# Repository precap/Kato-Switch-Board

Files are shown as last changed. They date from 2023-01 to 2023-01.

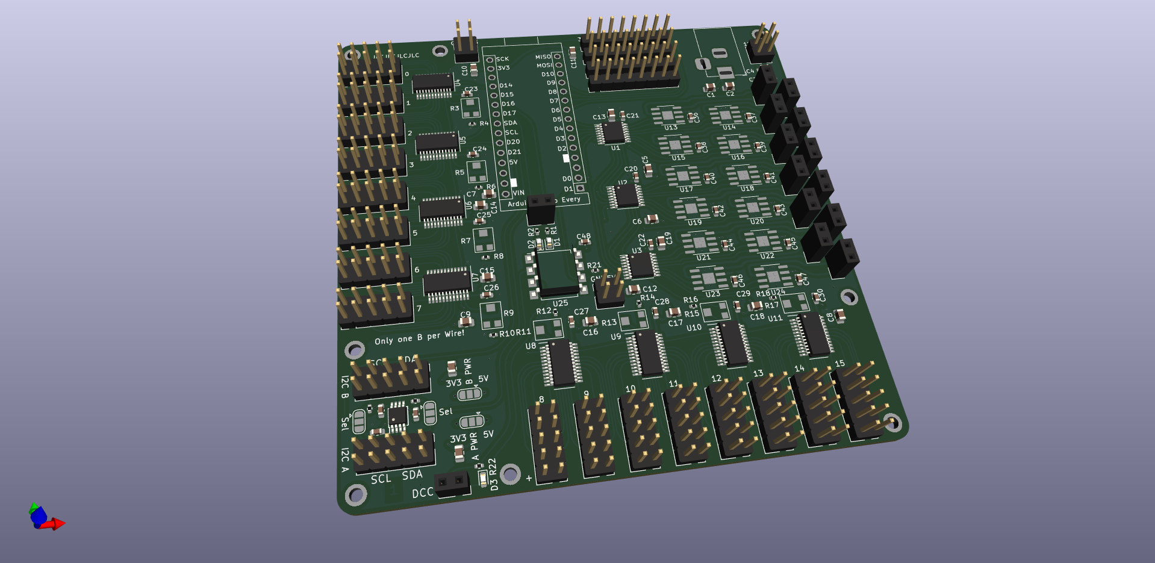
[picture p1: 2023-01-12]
kato-switch-board.png

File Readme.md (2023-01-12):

The board is designed to throw single solenoid switches (e.g. Kato N-scale switches), and serve as multipurpose Expansion to a DCC-EX setup.

# Software
to be written. Help welcome.

# Hardware
Created in KiCad 6.10. Supposedly all the symbol libraries are included in KiCad 6 Projects. I have never tested that though, so let me know if there are any problems with loading.

## Arduino Nano Every
The Board is designed to run with an Arduino Nano Every exclusively (Note: Arduino Nano Every is distinct from Arduino Nano).
This is a conscious Design Decision, as the Nano Every has all the power supply components on board to generate sufficient 3.3V and 5V amperage to power the entire board from the higher Voltage input over the Barrel Jack.
Warning: Do not attempt to run Arduino Nano or other pin compatible boards that cannot handle high voltage on the VIN pin.

## Power Supply
should be provided to the 2.1mm Barrel Jack, or to the pins beside it marked 12V. Voltage fed here will go directly to the switches, LEDs, and to the VIN pin in the Arduino Nano Footprint.
The Arduino Nano Every can provide 1A of 5V, and up to 0.5A of that can further be converted to 3.3V. Most of this capability will be unused and is made available on the marked 2x2 pin headers for external use.

## Board Features
### Switches
Support for 12 Switches. Switching is performed by PT5126A-H chips. Supposedly they can manage up to 2.8A (Kato Switch will draw 0.5A@12V, Double crossover 2A).
Connectors are standard 1x2 pins with 2.54mm spacing for now.

### LED
Up to 128 Output pins. Using SM16206S, which seem to be a knockoff of the (magnitudes more expensive) TLC59282DBQR.
The outermst pins on the connectors are power supply, the others connected to the outputs.

### I2C
A PCA9617ADPJ i2c repeater is fitted on the board, allowing the i2c bus to reach a greater area. The chip can also translate between different voltage levels on the i2c bus, jumpers to set the voltage are provided.

### DCC
DCC Input over an optocopler is possible.

### RFID
Up to four RC522 RFID Reader breakout boards can be connected. The pin arrangement matches commonly found breakout boards, allowing connection with a 8 pin cable.
Whether this feature is can be added to the software in a way that supports all 4 readers remains to be seen, as the RC522 must be polled continuously to detect passing RFID Tags.

## Evaluation Testing

All Evaluation Testing was only performed in a feature incomplete Prototype Version.

| Component | Status |
|---|---|
| Switch Drivers| OK |
| LED Drivers | tbd |
| I2C Repeater  | OK |
| DCC Circuitry | no hw  |
| RFID Reader | OK |

# Production
All SMD Components are available @ jlcpcb at time of release.
Production files can be found in `jlcbcb-production/`. Only the SMD-only assembly files are complete at time of release.
10 boards, assembled with SMD Coponents only, are around 125$ before shipping and taxes. Placing all the Pins will push this to 200$.

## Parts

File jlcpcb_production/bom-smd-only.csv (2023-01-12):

Designator | Footprint | Comment | LCSC Part Number
C1, C2, C3, C31, C35, C4, C5, C6, C7, C8, C9 | 0805 | 22u | C45783
C10, C11, C12, C13, C14, C15, C16, C17, C18, C19 | 0805 | 47u | C16780
C20, C21, C22, C23, C24, C25, C26, C27, C28, C29, C30, C32, C33, C34, C36, C37, C38, C39, C40, C41, C42, C43, C44, C45, C46, C47, C48 | 0603 | 100nf | C14663
D1, D2, D3 | 0603 | 0603_LED | C72043
R1, R10, R12, R14, R16, R18, R2, R22, R4, R6, R8 | 0402 | 2k2 | C25879
R11, R13, R15, R17, R3, R5, R7, R9 | SMD | VG039NCHXTB503 | C145161
R19, R20, R21 | 0402 | 10k | C25744
U1, U2, U3 | TSSOP-16 | 74HC238 | C60434
U10, U11, U4, U5, U6, U7, U8, U9 | QSOP-24 | SM16206 | C121618
U12 | TSSOP-8 | PCA9617ADPJ | C128388
U13, U14, U15, U16, U17, U18, U19, U20, U21, U22, U23, U24 | HSOP-8-1 | PT5126A | C782185
U25 | SSO-8 | 6N137 | C110020

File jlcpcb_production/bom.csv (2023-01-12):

Designator | Footprint | Comment | LCSC Part Number
C1, C2, C3, C31, C35, C4, C5, C6, C7, C8, C9 | 805 | 22u | C45783
C10, C11, C12, C13, C14, C15, C16, C17, C18, C19 | 805 | 47u | C16780
C20, C21, C22, C23, C24, C25, C26, C27, C28, C29, C30, C32, C33, C34, C36, C37, C38, C39, C40, C41, C42, C43, C44, C45, C46, C47, C48 | 603 | 100nf | C14663
D1, D2, D3 | 603 | 0603_LED | C72043
R1, R10, R12, R14, R16, R18, R2, R22, R4, R6, R8 | 402 | 2k2 | C25879
R11, R13, R15, R17, R3, R5, R7, R9 | SMD | VG039NCHXTB503 | C145161
R19, R20, R21 | 402 | 10k | C25744
U1, U2, U3 | TSSOP-16 | 74HC238 | C60434
U10, U11, U4, U5, U6, U7, U8, U9 | QSOP-24 | SM16206 | C121618
U12 | TSSOP-8 | PCA9617ADPJ | C128388
U13, U14, U15, U16, U17, U18, U19, U20, U21, U22, U23, U24 | HSOP-8-1 | PT5126A | C782185
U25 | SSO-8 | 6N137 | C110020
J1, J2, J3, J4 | PinHeader_1x08_P2.54mm_Vertical | Conn_01x08 | C358689
J10, J11, J12, J13, J14, J15, J16, J17, J18, J19, J20, J21, J22, J23, J24, J25, J26, J27 | PinHeader_2x05_P2.54mm_Vertical | Conn_02x05_Odd_Even | C492422
J28, J29, J30, J31, J32, J33, J34, J35, J36, J37, J38, J39, J40, J5 | PinSocket_1x02_P2.54mm_Vertical | Conn_01x02 | C492401
J6 | BarrelJack_Horizontal | Barrel_Jack_MountingPin | C16214
A1, A2 | PinHeader_1x15_P2.54mm_Vertical | Arduino Nano | C2932676

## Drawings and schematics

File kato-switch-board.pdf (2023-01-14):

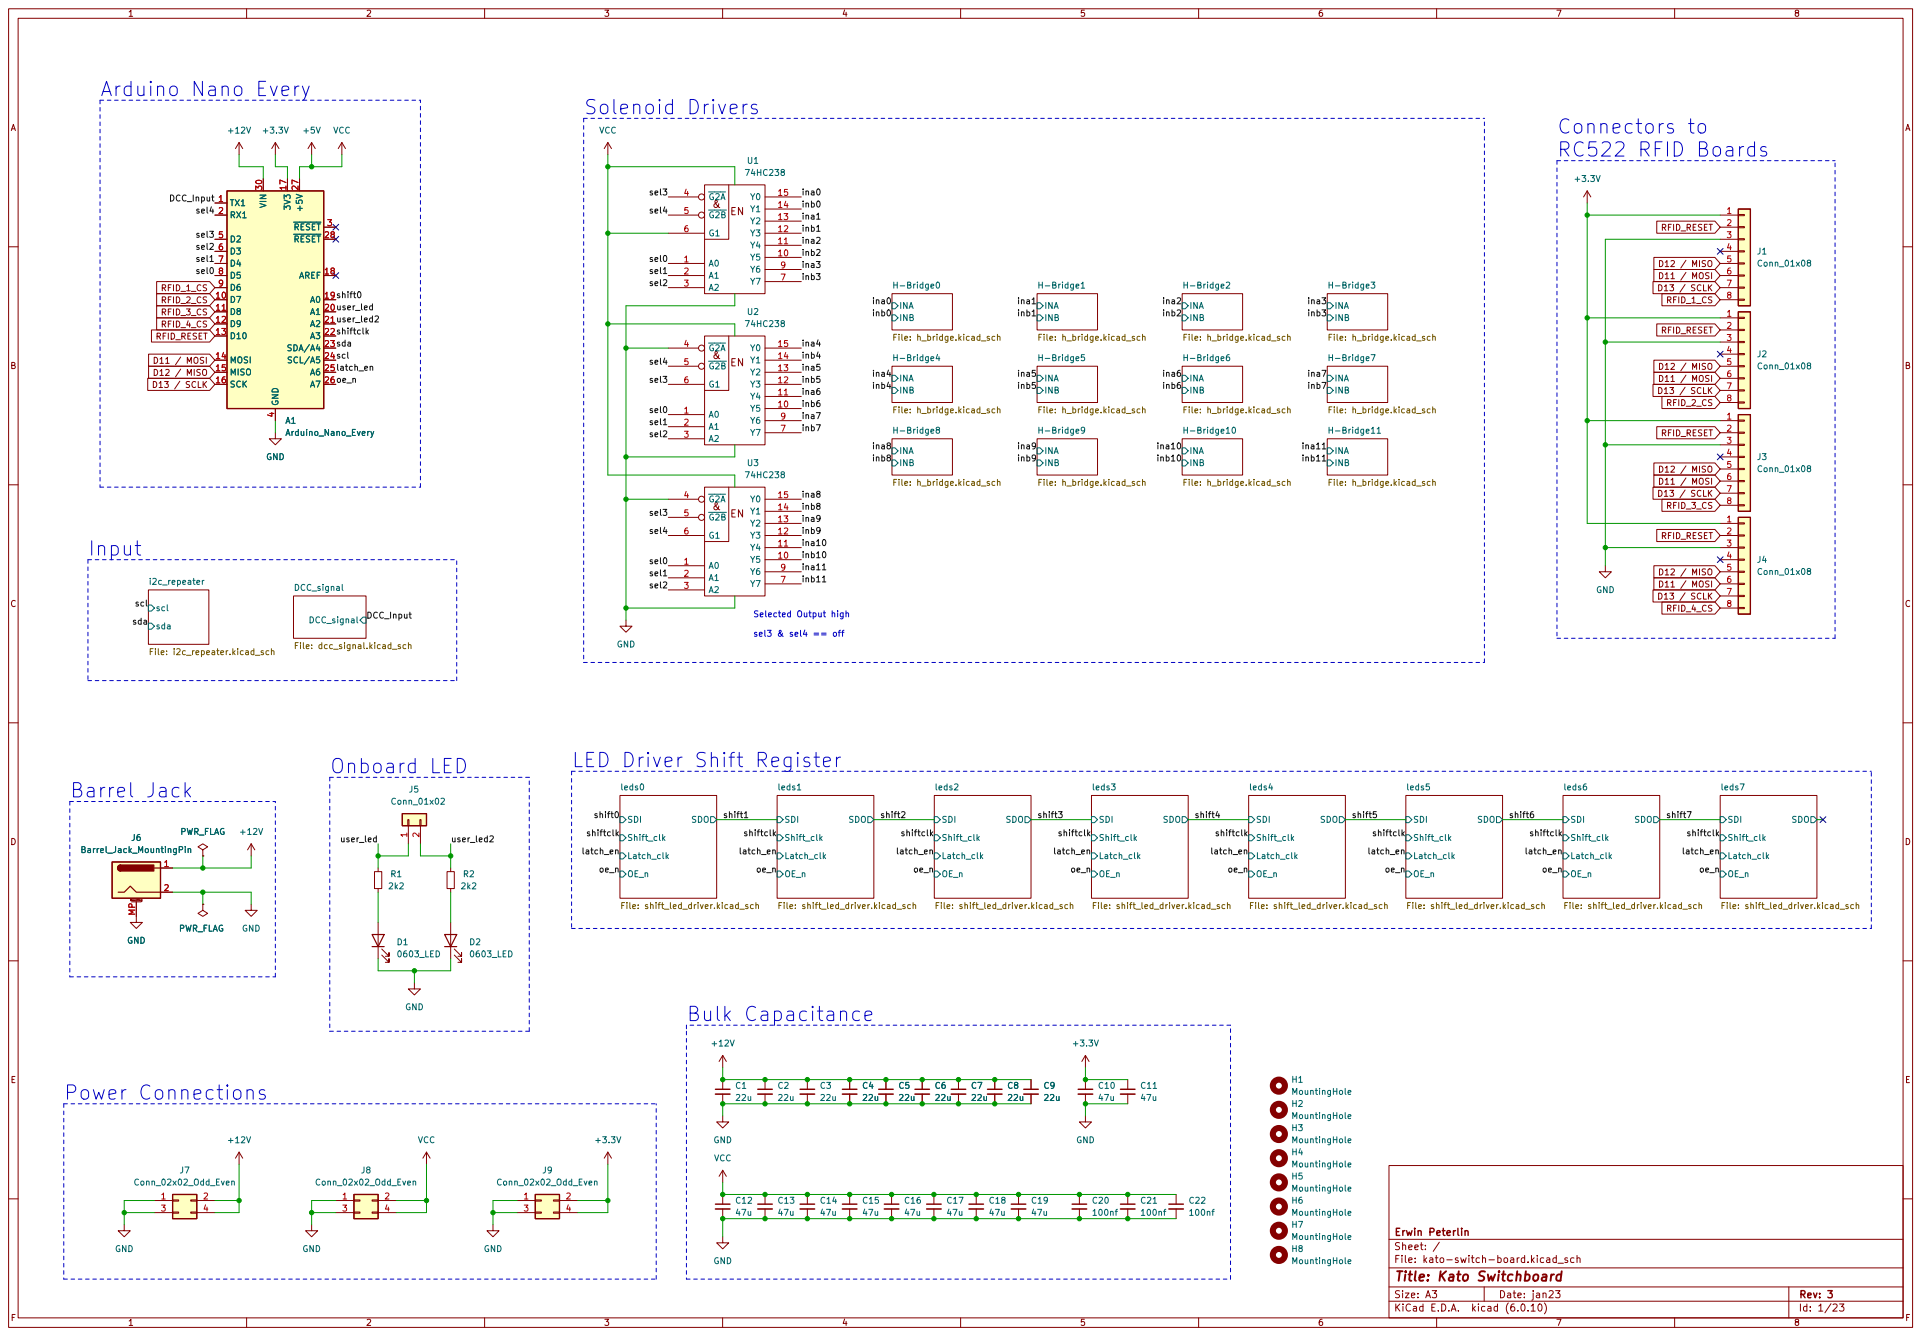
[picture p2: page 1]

File: kato-switch-board.kicad_sch Sheet: / Erwin Peterlin

Id: 1/23 Title: Kato Switchboard

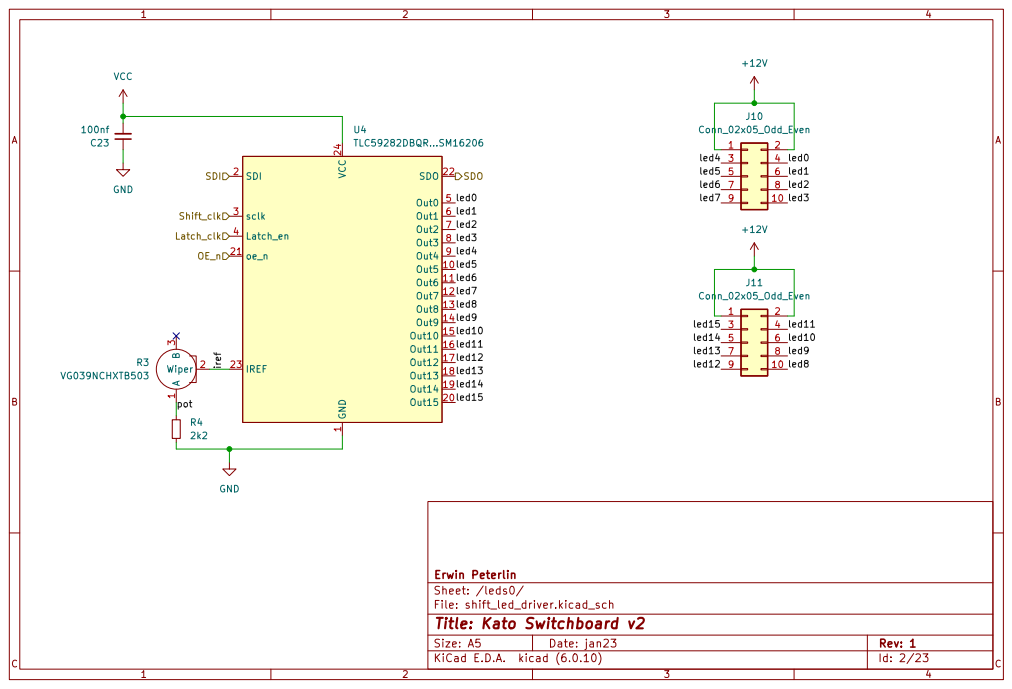
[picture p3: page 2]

File: shift_led_driver.kicad_sch Sheet: /leds0/ Erwin Peterlin C23

Id: 2/23 Title: Kato Switchboard v2

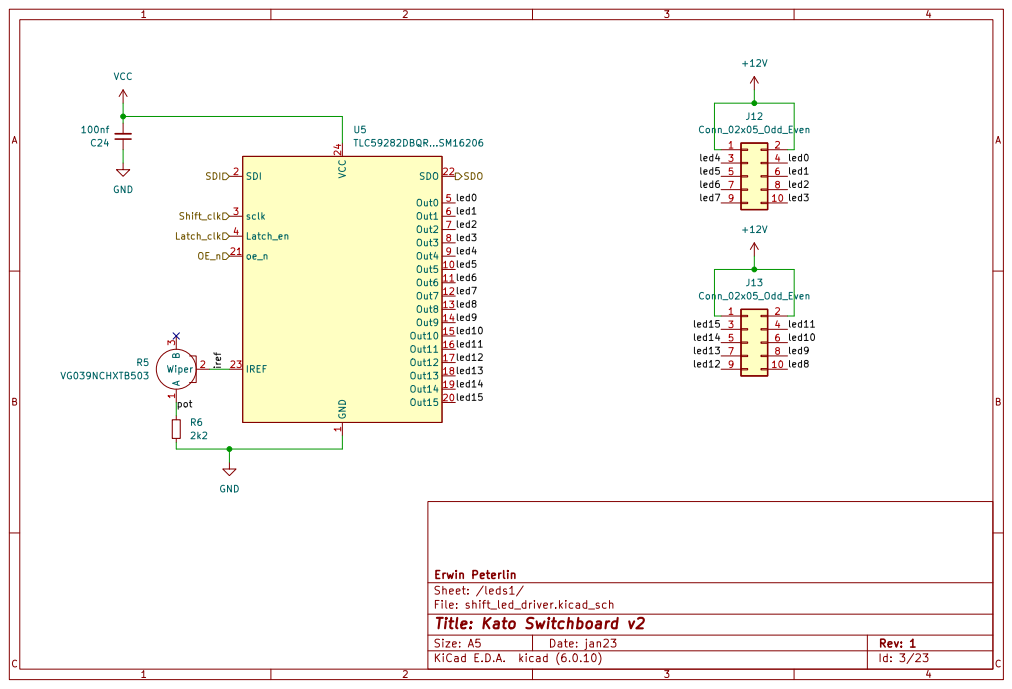
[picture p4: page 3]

File: shift_led_driver.kicad_sch Sheet: /leds1/ Erwin Peterlin C24

Id: 3/23 Title: Kato Switchboard v2

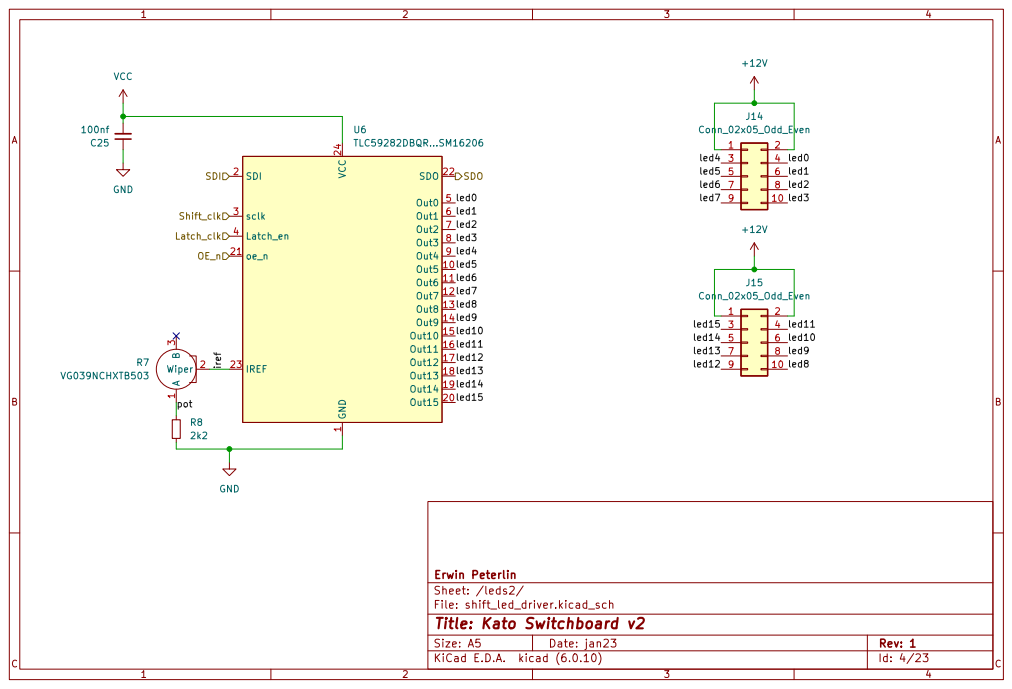
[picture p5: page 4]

File: shift_led_driver.kicad_sch Sheet: /leds2/ Erwin Peterlin C25

Id: 4/23 Title: Kato Switchboard v2

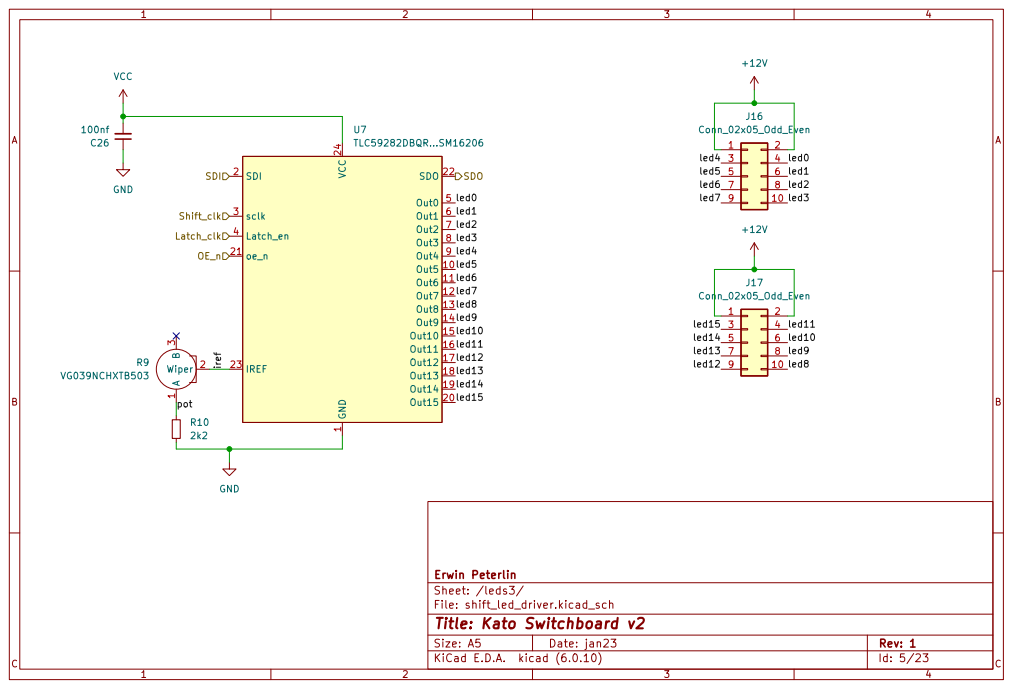
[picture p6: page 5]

File: shift_led_driver.kicad_sch Sheet: /leds3/ Erwin Peterlin C26

Id: 5/23 Title: Kato Switchboard v2

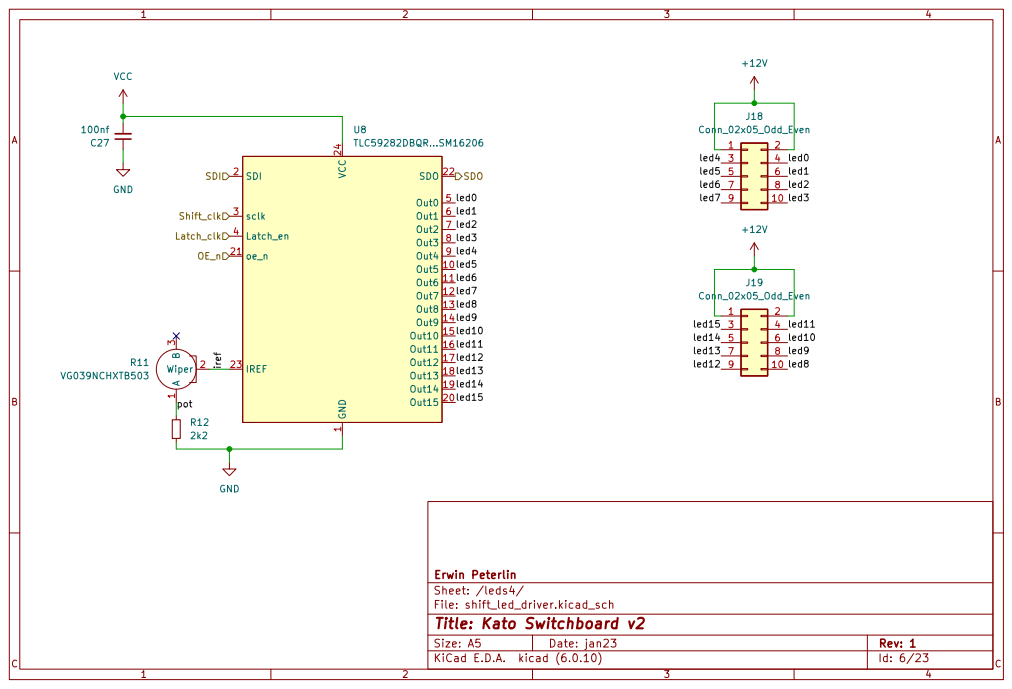
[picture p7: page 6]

File: shift_led_driver.kicad_sch Sheet: /leds4/ Erwin Peterlin C27

Id: 6/23 Title: Kato Switchboard v2

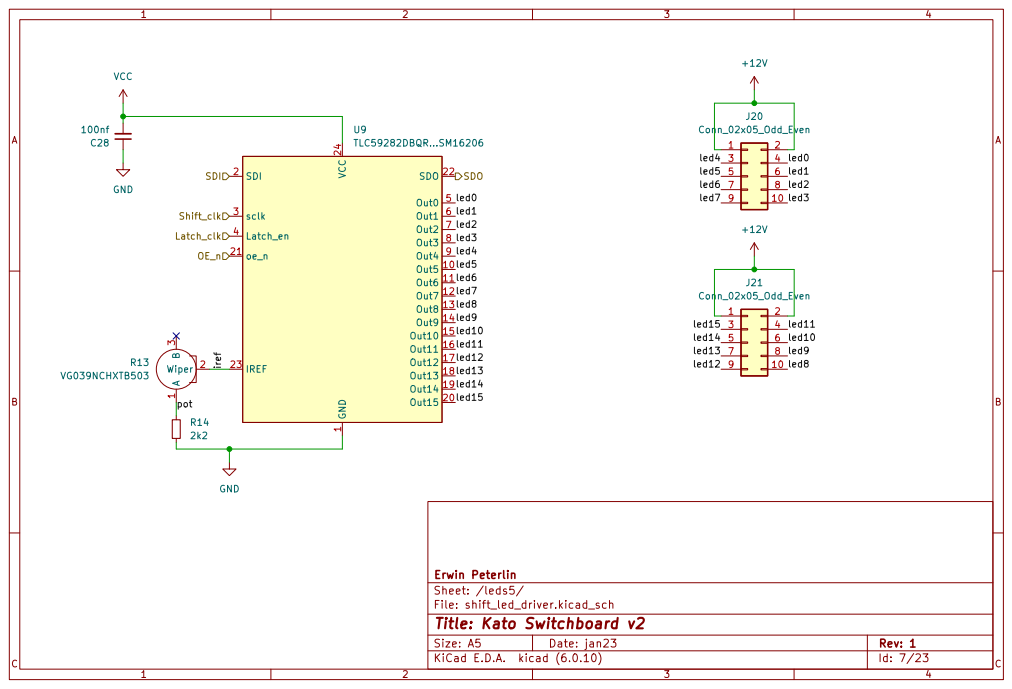
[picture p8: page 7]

File: shift_led_driver.kicad_sch Sheet: /leds5/ Erwin Peterlin C28

Id: 7/23 Title: Kato Switchboard v2

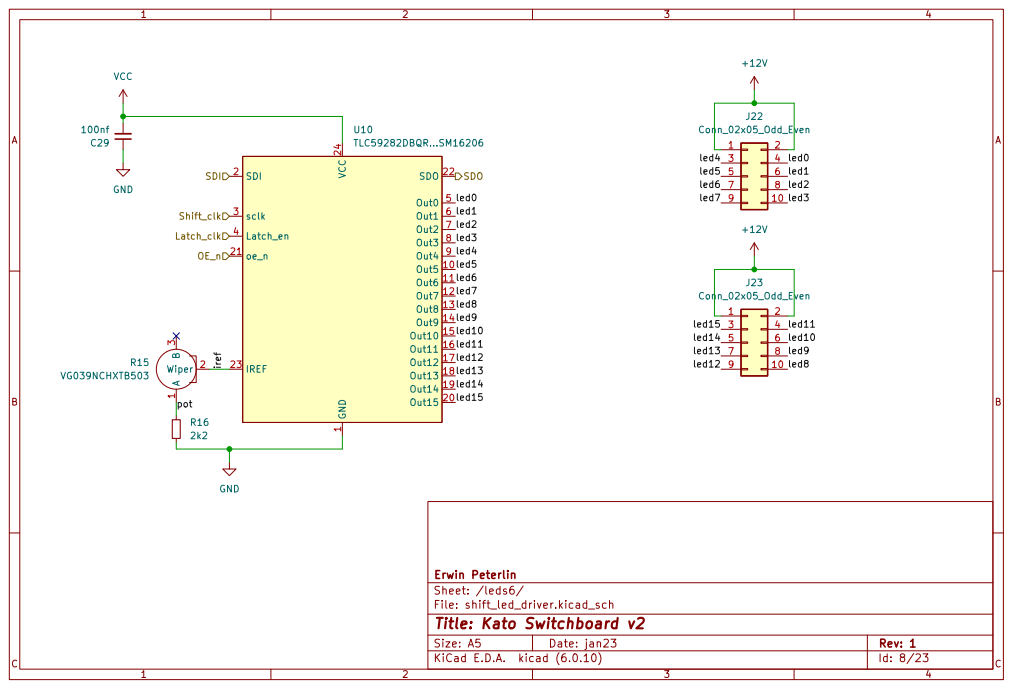
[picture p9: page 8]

File: shift_led_driver.kicad_sch Sheet: /leds6/ Erwin Peterlin C29

Id: 8/23 Title: Kato Switchboard v2

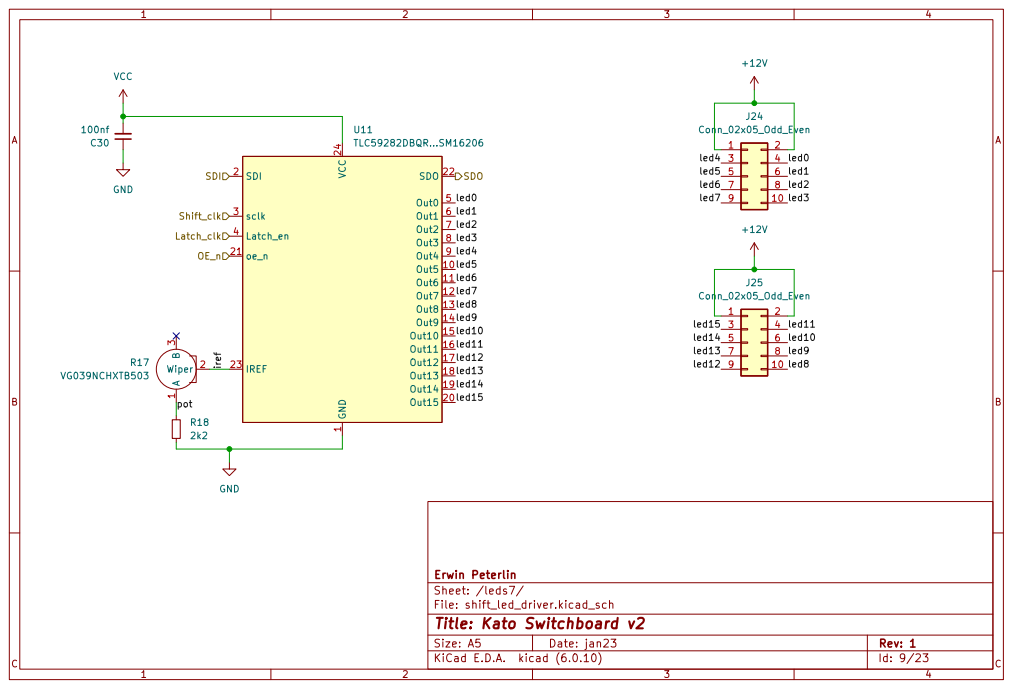
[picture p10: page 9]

File: shift_led_driver.kicad_sch Sheet: /leds7/ Erwin Peterlin C30

Id: 9/23 Title: Kato Switchboard v2

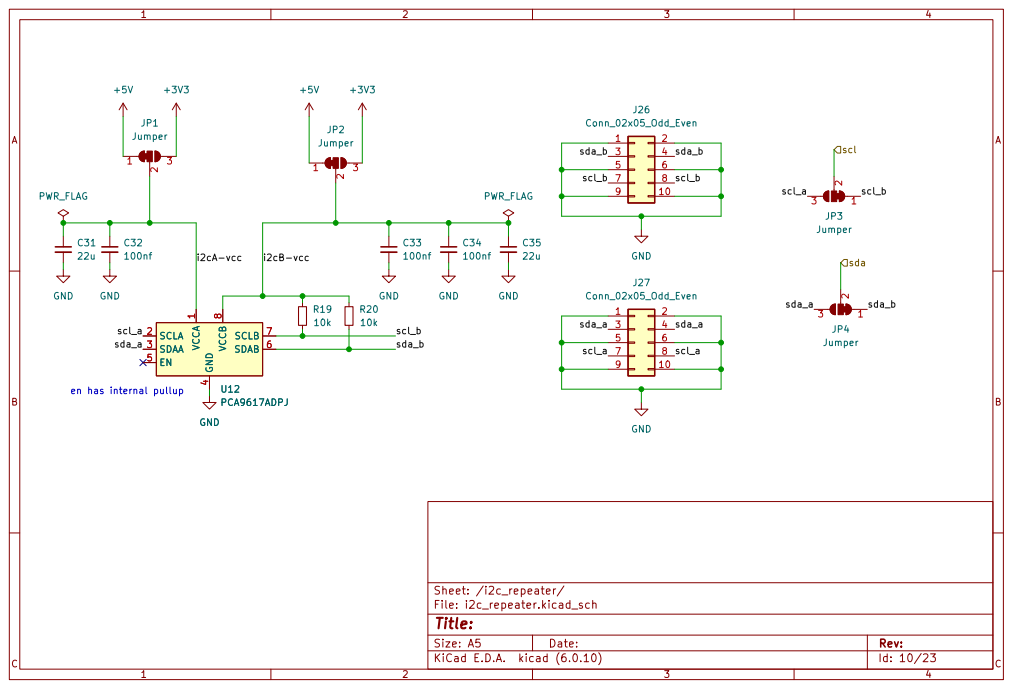
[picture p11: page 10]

sda_b 3 5 | 4 sda_b 6

scl_b 7 9 | 8 scl_b 10

4 EN 5 SDAB 6 SCLB 7 VCCB

sda_a 3 5 | sda_a 4 6

scl_a 7 9 | 8 scl_a 10

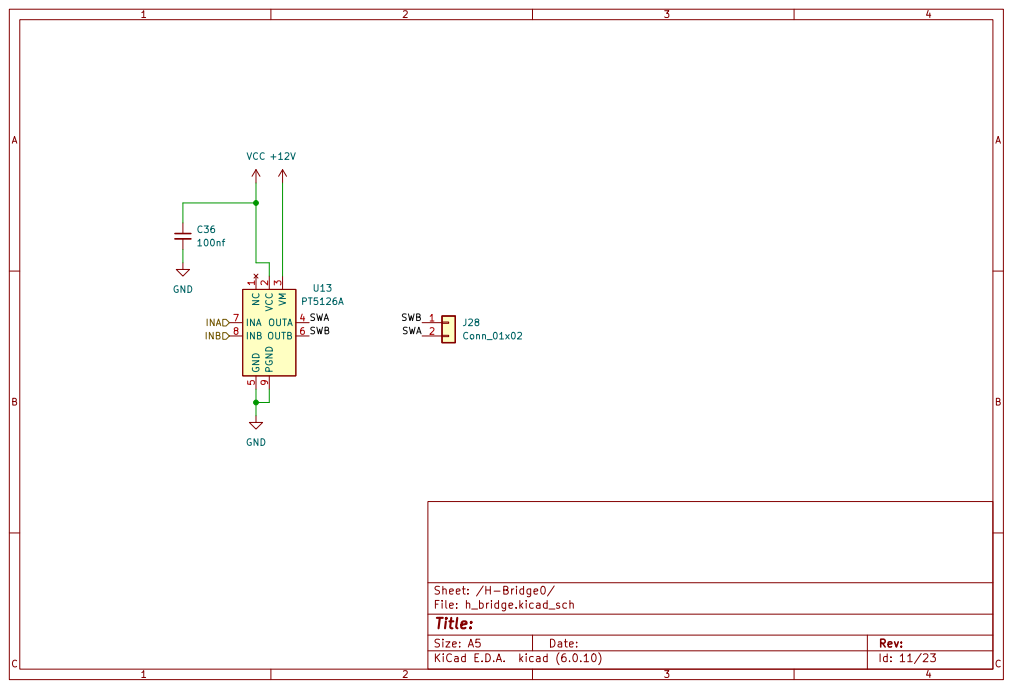
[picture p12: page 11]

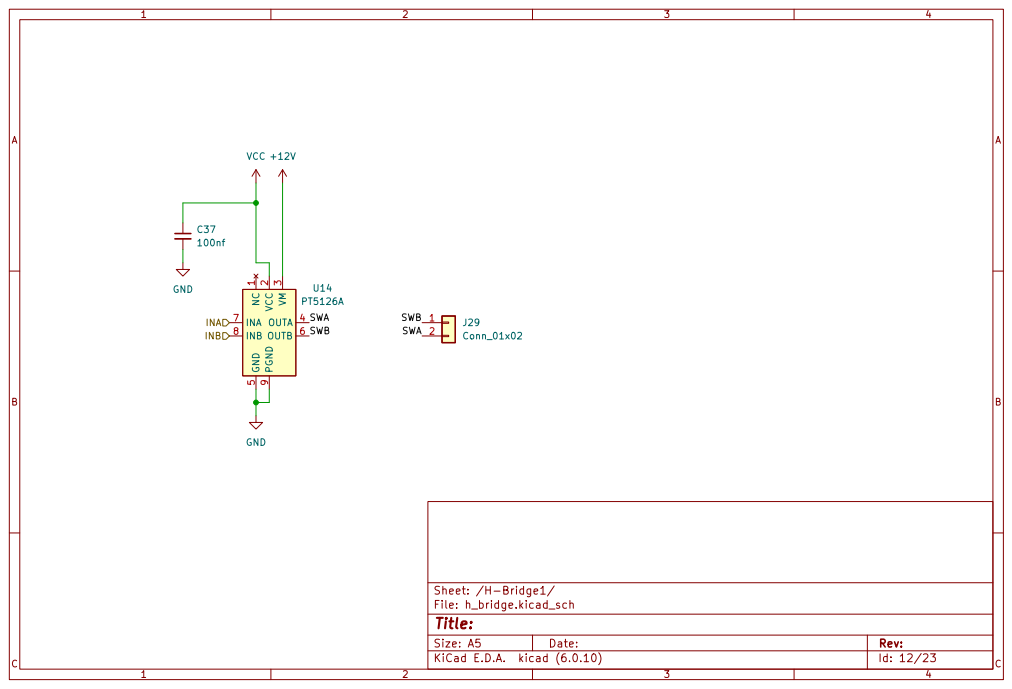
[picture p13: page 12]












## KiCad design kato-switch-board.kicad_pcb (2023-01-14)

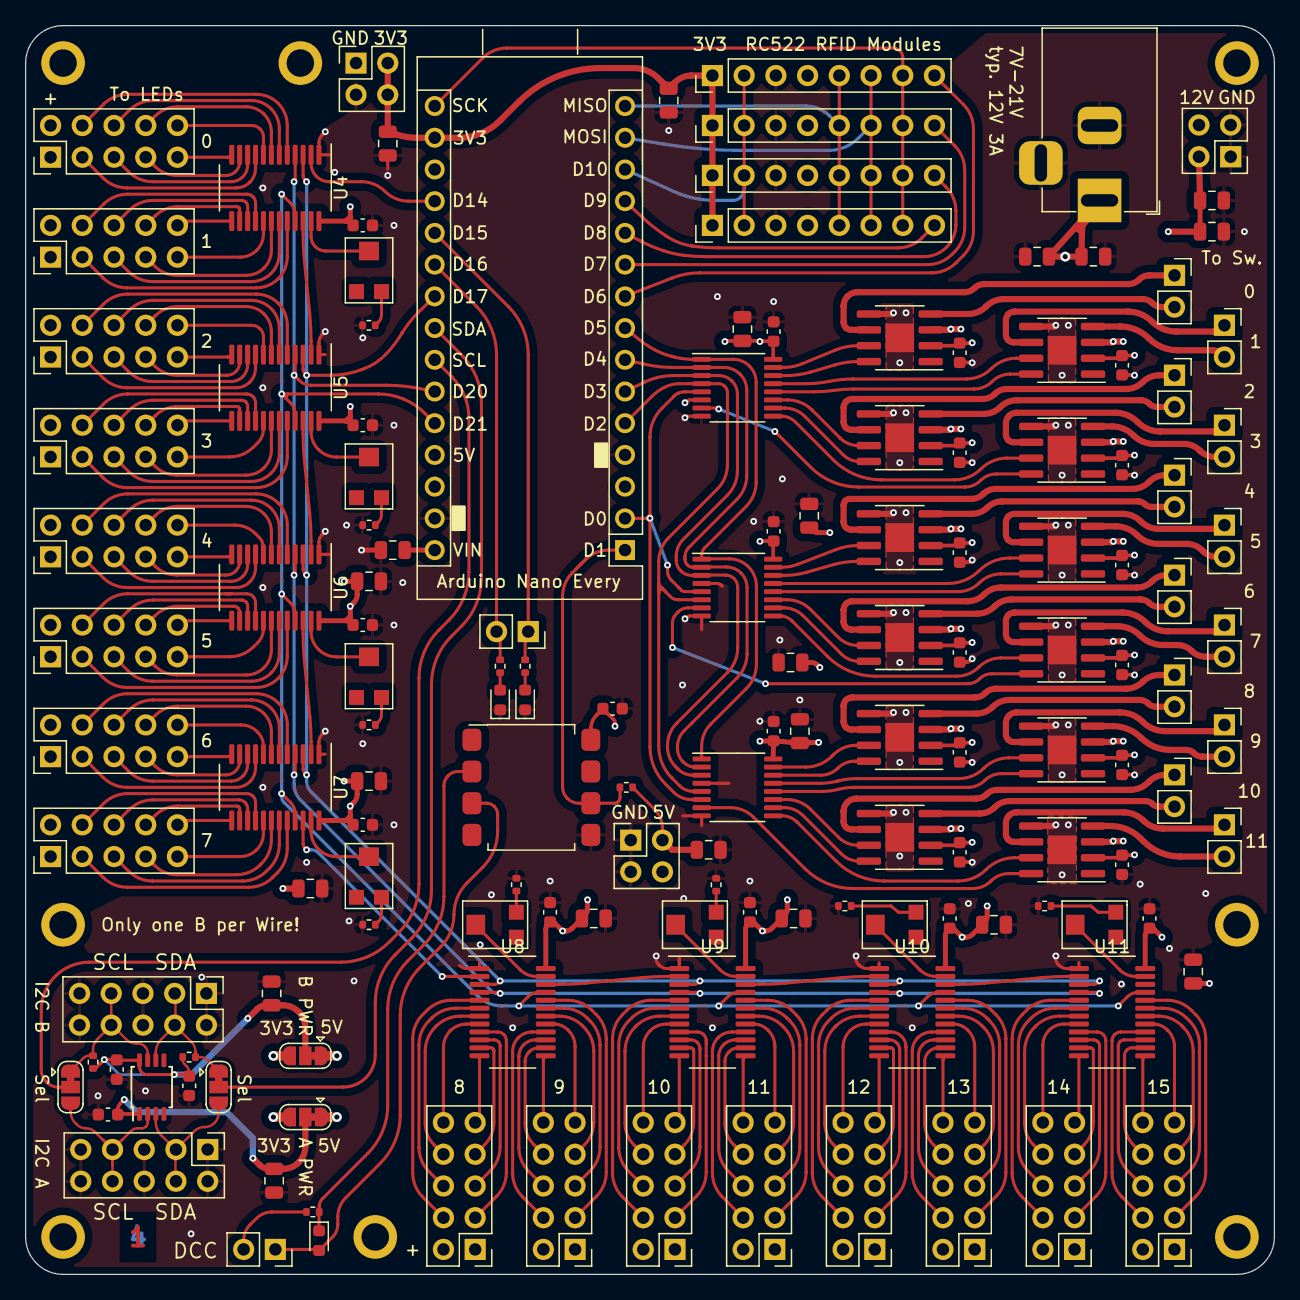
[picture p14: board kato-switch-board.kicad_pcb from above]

Board: 4 copper layers, 100.0 x 100.0 mm, 151 parts (0 on the bottom side), 236 nets.

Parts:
A1: Arduino_Nano_Every; Arduino_Nano
C1, C2, C3, C4, C5, C6, C7, C8, C9, C31, C35: 22u; C_0805_2012Metric
C10, C11, C12, C13, C14, C15, C16, C17, C18, C19: 47u; C_0805_2012Metric
C20, C21, C22, C23, C24, C25, C26, C27, C28, C29, C30, C32, C33, C34, C36, C37, C38, C39, C40, C41, C42, C43, C44, C45, C46, C47, C48: 100nf; C_0603_1608Metric
D1, D2, D3: 0603_LED; LED_0603_1608Metric
H1, H2, H3, H4, H5, H6, H7, H8: MountingHole; MountingHole_2.2mm_M2_ISO7380_Pad
J1, J2, J3, J4: Conn_01x08; PinHeader_1x08_P2.54mm_Vertical
J5, J28, J29, J30, J31, J32, J33, J34, J35, J36, J37, J38, J39, J40: Conn_01x02; PinSocket_1x02_P2.54mm_Vertical
J6: Barrel_Jack_MountingPin; BarrelJack_Horizontal
J7, J8, J9: Conn_02x02_Odd_Even; PinHeader_2x02_P2.54mm_Vertical
J10, J11, J12, J13, J14, J15, J16, J17, J18, J19, J20, J21, J22, J23, J24, J25, J26, J27: Conn_02x05_Odd_Even; PinHeader_2x05_P2.54mm_Vertical
JP1, JP2, JP3, JP4: Jumper; SolderJumper-3_P1.3mm_Bridged12_RoundedPad1.0x1.5mm
R1, R2, R4, R6, R8, R10, R12, R14, R16, R18, R22: 2k2; R_0402_1005Metric
R3, R5, R7, R9, R11, R13, R15, R17: VG039NCHXTB503; VG039NCHXT
R19, R20, R21: 10k; R_0402_1005Metric
U1, U2, U3: 74HC238; TSSOP-16_4.4x5mm_P0.65mm
U4, U5, U6, U7, U8, U9, U10, U11: TLC59282DBQR...SM16206; QSOP-24_3.9x8.7mm_P0.635mm_rounded_pads
U12: PCA9617ADPJ; TSSOP-8_3x3mm_P0.65mm
U13, U14, U15, U16, U17, U18, U19, U20, U21, U22, U23, U24: PT5126A; HSOP-8-1EP_3.9x4.9mm_P1.27mm_EP2.3x2.3mm
U25: 6N137; SSO-8_6.7x9.8mm_P2.54mm_Clearance8mm

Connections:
+3V3: A1.17 (3V3), C10.1, C11.1, J1.1, J2.1, J3.1, J4.1, J9.2, J9.4, JP1.3 (B), JP2.3 (B)
+5V: A1.27 (+5V), C12.1, C13.1, C14.1, C15.1, C16.1, C17.1, C18.1, C19.1, C20.1, C21.1, C22.1, C23.2, C24.2, C25.2, C26.2, C27.2, C28.2, C29.2, C30.2, C36.1, C37.1, C38.1, C39.1, C40.1, C41.1, C42.1, C43.1, C44.1, C45.1, C46.1, C47.1, C48.1, J8.2, J8.4, JP1.1 (A), JP2.1 (A), R21.2, U1.6 (G1), U1.16 (VCC), U2.16 (VCC), U3.16 (VCC), U4.24 (VCC), U5.24 (VCC), U6.24 (VCC), U7.24 (VCC), U8.24 (VCC), U9.24 (VCC), U10.24 (VCC), U11.24 (VCC), U13.2 (VCC), U14.2 (VCC), U15.2 (VCC), U16.2 (VCC), U17.2 (VCC), U18.2 (VCC), U19.2 (VCC), U20.2 (VCC), U21.2 (VCC), U22.2 (VCC), U23.2 (VCC), U24.2 (VCC), U25.8 (VCC)
+12V: A1.30 (VIN), C1.1, C2.1, C3.1, C4.1, C5.1, C6.1, C7.1, C8.1, C9.1, J6.1, J7.2, J7.4, J10.1, J10.2, J11.1, J11.2, J12.1, J12.2, J13.1, J13.2, J14.1, J14.2, J15.1, J15.2, J16.1, J16.2, J17.1, J17.2, J18.1, J18.2, J19.1, J19.2, J20.1, J20.2, J21.1, J21.2, J22.1, J22.2, J23.1, J23.2, J24.1, J24.2, J25.1, J25.2, U13.3 (VM), U14.3 (VM), U15.3 (VM), U16.3 (VM), U17.3 (VM), U18.3 (VM), U19.3 (VM), U20.3 (VM), U21.3 (VM), U22.3 (VM), U23.3 (VM), U24.3 (VM)
/DCC_Input: A1.1 (TX1), R21.1, U25.6 (VO)
/DCC_signal/DCC_W1: J40.2, R22.2
/DCC_signal/DCC_W1_R: D3.1 (K), R22.1, U25.2 (A)
/DCC_signal/DCC_W2: D3.2 (A), J40.1, U25.3 (C)
/H-Bridge0/SWA: J28.2, U13.4 (OUTA)
/H-Bridge0/SWB: J28.1, U13.6 (OUTB)
/H-Bridge1/SWA: J29.2, U14.4 (OUTA)
/H-Bridge1/SWB: J29.1, U14.6 (OUTB)
/H-Bridge2/SWA: J30.2, U15.4 (OUTA)
/H-Bridge2/SWB: J30.1, U15.6 (OUTB)
/H-Bridge3/SWA: J31.2, U16.4 (OUTA)
/H-Bridge3/SWB: J31.1, U16.6 (OUTB)
/H-Bridge4/SWA: J32.2, U17.4 (OUTA)
/H-Bridge4/SWB: J32.1, U17.6 (OUTB)
/H-Bridge5/SWA: J33.2, U18.4 (OUTA)
/H-Bridge5/SWB: J33.1, U18.6 (OUTB)
/H-Bridge6/SWA: J34.2, U19.4 (OUTA)
/H-Bridge6/SWB: J34.1, U19.6 (OUTB)
/H-Bridge7/SWA: J35.2, U20.4 (OUTA)
/H-Bridge7/SWB: J35.1, U20.6 (OUTB)
/H-Bridge8/SWA: J36.2, U21.4 (OUTA)
/H-Bridge8/SWB: J36.1, U21.6 (OUTB)
/H-Bridge9/SWA: J37.2, U22.4 (OUTA)
/H-Bridge9/SWB: J37.1, U22.6 (OUTB)
/H-Bridge10/SWA: J38.2, U23.4 (OUTA)
/H-Bridge10/SWB: J38.1, U23.6 (OUTB)
/H-Bridge11/SWA: J39.2, U24.4 (OUTA)
/H-Bridge11/SWB: J39.1, U24.6 (OUTB)
/i2c_repeater/i2cA-vcc: C31.1, C32.1, JP1.2 (C), U12.1 (VCCA)
/i2c_repeater/i2cB-vcc: C33.1, C34.1, C35.1, JP2.2 (C), R19.2, R20.2, U12.8 (VCCB)
/i2c_repeater/scl_a: J27.7, J27.8, JP3.3 (B), U12.2 (SCLA)
/i2c_repeater/scl_b: J26.7, J26.8, JP3.1 (A), R19.1, U12.7 (SCLB)
/i2c_repeater/sda_a: J27.3, J27.4, JP4.3 (B), U12.3 (SDAA)
/i2c_repeater/sda_b: J26.3, J26.4, JP4.1 (A), R20.1, U12.6 (SDAB)
/ina0: U1.15 (Y0), U13.7 (INA)
/ina1: U1.13 (Y2), U14.7 (INA)
/ina2: U1.11 (Y4), U15.7 (INA)
/ina3: U1.9 (Y6), U16.7 (INA)
/ina4: U2.15 (Y0), U17.7 (INA)
/ina5: U2.13 (Y2), U18.7 (INA)
/ina6: U2.11 (Y4), U19.7 (INA)
/ina7: U2.9 (Y6), U20.7 (INA)
/ina8: U3.15 (Y0), U21.7 (INA)
/ina9: U3.13 (Y2), U22.7 (INA)
/ina10: U3.11 (Y4), U23.7 (INA)
/ina11: U3.9 (Y6), U24.7 (INA)
/inb0: U1.14 (Y1), U13.8 (INB)
/inb1: U1.12 (Y3), U14.8 (INB)
/inb2: U1.10 (Y5), U15.8 (INB)
/inb3: U1.7 (Y7), U16.8 (INB)
/inb4: U2.14 (Y1), U17.8 (INB)
/inb5: U2.12 (Y3), U18.8 (INB)
/inb6: U2.10 (Y5), U19.8 (INB)
/inb7: U2.7 (Y7), U20.8 (INB)
/inb8: U3.14 (Y1), U21.8 (INB)
/inb9: U3.12 (Y3), U22.8 (INB)
/inb10: U3.10 (Y5), U23.8 (INB)
/inb11: U3.7 (Y7), U24.8 (INB)
/latch_en: A1.25 (A6), U4.4 (Latch_en), U5.4 (Latch_en), U6.4 (Latch_en), U7.4 (Latch_en), U8.4 (Latch_en), U9.4 (Latch_en), U10.4 (Latch_en), U11.4 (Latch_en)
/leds0/iref: R3.2 (Wiper), U4.23 (IREF)
/leds0/led0: J10.4, U4.5 (Out0)
/leds0/led1: J10.6, U4.6 (Out1)
/leds0/led2: J10.8, U4.7 (Out2)
/leds0/led3: J10.10, U4.8 (Out3)
/leds0/led4: J10.3, U4.9 (Out4)
/leds0/led5: J10.5, U4.10 (Out5)
/leds0/led6: J10.7, U4.11 (Out6)
/leds0/led7: J10.9, U4.12 (Out7)
/leds0/led8: J11.10, U4.13 (Out8)
/leds0/led9: J11.8, U4.14 (Out9)
/leds0/led10: J11.6, U4.15 (Out10)
/leds0/led11: J11.4, U4.16 (Out11)
/leds0/led12: J11.9, U4.17 (Out12)
/leds0/led13: J11.7, U4.18 (Out13)
/leds0/led14: J11.5, U4.19 (Out14)
/leds0/led15: J11.3, U4.20 (Out15)
/leds0/pot: R3.1 (A), R4.1
/leds1/iref: R5.2 (Wiper), U5.23 (IREF)
/leds1/led0: J12.4, U5.5 (Out0)
/leds1/led1: J12.6, U5.6 (Out1)
/leds1/led2: J12.8, U5.7 (Out2)
/leds1/led3: J12.10, U5.8 (Out3)
/leds1/led4: J12.3, U5.9 (Out4)
/leds1/led5: J12.5, U5.10 (Out5)
/leds1/led6: J12.7, U5.11 (Out6)
/leds1/led7: J12.9, U5.12 (Out7)
/leds1/led8: J13.10, U5.13 (Out8)
/leds1/led9: J13.8, U5.14 (Out9)
/leds1/led10: J13.6, U5.15 (Out10)
/leds1/led11: J13.4, U5.16 (Out11)
/leds1/led12: J13.9, U5.17 (Out12)
/leds1/led13: J13.7, U5.18 (Out13)
/leds1/led14: J13.5, U5.19 (Out14)
/leds1/led15: J13.3, U5.20 (Out15)
/leds1/pot: R5.1 (A), R6.1
/leds2/iref: R7.2 (Wiper), U6.23 (IREF)
/leds2/led0: J14.4, U6.5 (Out0)
/leds2/led1: J14.6, U6.6 (Out1)
/leds2/led2: J14.8, U6.7 (Out2)
/leds2/led3: J14.10, U6.8 (Out3)
/leds2/led4: J14.3, U6.9 (Out4)
/leds2/led5: J14.5, U6.10 (Out5)
/leds2/led6: J14.7, U6.11 (Out6)
/leds2/led7: J14.9, U6.12 (Out7)
/leds2/led8: J15.10, U6.13 (Out8)
/leds2/led9: J15.8, U6.14 (Out9)
/leds2/led10: J15.6, U6.15 (Out10)
/leds2/led11: J15.4, U6.16 (Out11)
/leds2/led12: J15.9, U6.17 (Out12)
/leds2/led13: J15.7, U6.18 (Out13)
/leds2/led14: J15.5, U6.19 (Out14)
/leds2/led15: J15.3, U6.20 (Out15)
/leds2/pot: R7.1 (A), R8.1
/leds3/iref: R9.2 (Wiper), U7.23 (IREF)
/leds3/led0: J16.4, U7.5 (Out0)
/leds3/led1: J16.6, U7.6 (Out1)
/leds3/led2: J16.8, U7.7 (Out2)
/leds3/led3: J16.10, U7.8 (Out3)
/leds3/led4: J16.3, U7.9 (Out4)
/leds3/led5: J16.5, U7.10 (Out5)
/leds3/led6: J16.7, U7.11 (Out6)
/leds3/led7: J16.9, U7.12 (Out7)
/leds3/led8: J17.10, U7.13 (Out8)
/leds3/led9: J17.8, U7.14 (Out9)
/leds3/led10: J17.6, U7.15 (Out10)
/leds3/led11: J17.4, U7.16 (Out11)
/leds3/led12: J17.9, U7.17 (Out12)
/leds3/led13: J17.7, U7.18 (Out13)
/leds3/led14: J17.5, U7.19 (Out14)
/leds3/led15: J17.3, U7.20 (Out15)
/leds3/pot: R9.1 (A), R10.1
/leds4/iref: R11.2 (Wiper), U8.23 (IREF)
/leds4/led0: J18.4, U8.5 (Out0)
/leds4/led1: J18.6, U8.6 (Out1)
/leds4/led2: J18.8, U8.7 (Out2)
/leds4/led3: J18.10, U8.8 (Out3)
/leds4/led4: J18.3, U8.9 (Out4)
/leds4/led5: J18.5, U8.10 (Out5)
/leds4/led6: J18.7, U8.11 (Out6)
/leds4/led7: J18.9, U8.12 (Out7)
/leds4/led8: J19.10, U8.13 (Out8)
/leds4/led9: J19.8, U8.14 (Out9)
/leds4/led10: J19.6, U8.15 (Out10)
/leds4/led11: J19.4, U8.16 (Out11)
/leds4/led12: J19.9, U8.17 (Out12)
/leds4/led13: J19.7, U8.18 (Out13)
/leds4/led14: J19.5, U8.19 (Out14)
/leds4/led15: J19.3, U8.20 (Out15)
/leds4/pot: R11.1 (A), R12.1
/leds5/iref: R13.2 (Wiper), U9.23 (IREF)
/leds5/led0: J20.4, U9.5 (Out0)
/leds5/led1: J20.6, U9.6 (Out1)
/leds5/led2: J20.8, U9.7 (Out2)
/leds5/led3: J20.10, U9.8 (Out3)
/leds5/led4: J20.3, U9.9 (Out4)
/leds5/led5: J20.5, U9.10 (Out5)
/leds5/led6: J20.7, U9.11 (Out6)
/leds5/led7: J20.9, U9.12 (Out7)
/leds5/led8: J21.10, U9.13 (Out8)
/leds5/led9: J21.8, U9.14 (Out9)
/leds5/led10: J21.6, U9.15 (Out10)
/leds5/led11: J21.4, U9.16 (Out11)
/leds5/led12: J21.9, U9.17 (Out12)
/leds5/led13: J21.7, U9.18 (Out13)
/leds5/led14: J21.5, U9.19 (Out14)
/leds5/led15: J21.3, U9.20 (Out15)
/leds5/pot: R13.1 (A), R14.1
/leds6/iref: R15.2 (Wiper), U10.23 (IREF)
/leds6/led0: J22.4, U10.5 (Out0)
/leds6/led1: J22.6, U10.6 (Out1)
/leds6/led2: J22.8, U10.7 (Out2)
/leds6/led3: J22.10, U10.8 (Out3)
/leds6/led4: J22.3, U10.9 (Out4)
/leds6/led5: J22.5, U10.10 (Out5)
/leds6/led6: J22.7, U10.11 (Out6)
/leds6/led7: J22.9, U10.12 (Out7)
/leds6/led8: J23.10, U10.13 (Out8)
/leds6/led9: J23.8, U10.14 (Out9)
/leds6/led10: J23.6, U10.15 (Out10)
/leds6/led11: J23.4, U10.16 (Out11)
/leds6/led12: J23.9, U10.17 (Out12)
/leds6/led13: J23.7, U10.18 (Out13)
/leds6/led14: J23.5, U10.19 (Out14)
/leds6/led15: J23.3, U10.20 (Out15)
/leds6/pot: R15.1 (A), R16.1
/leds7/iref: R17.2 (Wiper), U11.23 (IREF)
/leds7/led0: J24.4, U11.5 (Out0)
/leds7/led1: J24.6, U11.6 (Out1)
/leds7/led2: J24.8, U11.7 (Out2)
/leds7/led3: J24.10, U11.8 (Out3)
/leds7/led4: J24.3, U11.9 (Out4)
/leds7/led5: J24.5, U11.10 (Out5)
/leds7/led6: J24.7, U11.11 (Out6)
/leds7/led7: J24.9, U11.12 (Out7)
/leds7/led8: J25.10, U11.13 (Out8)
/leds7/led9: J25.8, U11.14 (Out9)
/leds7/led10: J25.6, U11.15 (Out10)
/leds7/led11: J25.4, U11.16 (Out11)
/leds7/led12: J25.9, U11.17 (Out12)
/leds7/led13: J25.7, U11.18 (Out13)
/leds7/led14: J25.5, U11.19 (Out14)
/leds7/led15: J25.3, U11.20 (Out15)
/leds7/pot: R17.1 (A), R18.1
/oe_n: A1.26 (A7), U4.21 (oe_n), U5.21 (oe_n), U6.21 (oe_n), U7.21 (oe_n), U8.21 (oe_n), U9.21 (oe_n), U10.21 (oe_n), U11.21 (oe_n)
/scl: A1.24 (SCL/A5), JP3.2 (C)
/sda: A1.23 (SDA/A4), JP4.2 (C)
/sel0: A1.8 (D5), U1.1 (A0), U2.1 (A0), U3.1 (A0)
/sel1: A1.7 (D4), U1.2 (A1), U2.2 (A1), U3.2 (A1)
/sel2: A1.6 (D3), U1.3 (A2), U2.3 (A2), U3.3 (A2)
/sel3: A1.5 (D2), U1.4 (~G2A), U2.6 (G1), U3.5 (~G2B)
/sel4: A1.2 (RX1), U1.5 (~G2B), U2.5 (~G2B), U3.6 (G1)
/shift0: A1.19 (A0), U4.2 (SDI)
/shift1: U4.22 (SDO), U5.2 (SDI)
/shift2: U5.22 (SDO), U6.2 (SDI)
/shift3: U6.22 (SDO), U7.2 (SDI)
/shift4: U7.22 (SDO), U8.2 (SDI)
/shift5: U8.22 (SDO), U9.2 (SDI)
/shift6: U9.22 (SDO), U10.2 (SDI)
/shift7: U10.22 (SDO), U11.2 (SDI)
/shiftclk: A1.22 (A3), U4.3 (sclk), U5.3 (sclk), U6.3 (sclk), U7.3 (sclk), U8.3 (sclk), U9.3 (sclk), U10.3 (sclk), U11.3 (sclk)
/user_led: A1.20 (A1), J5.1, R1.2
/user_led2: A1.21 (A2), J5.2, R2.2
D11 / MOSI: A1.14 (MOSI), J1.6, J2.6, J3.6, J4.6
D12 / MISO: A1.15 (MISO), J1.5, J2.5, J3.5, J4.5
D13 / SCLK: A1.16 (SCK), J1.7, J2.7, J3.7, J4.7
GND: A1.4 (GND), A1.29 (GND), C1.2, C2.2, C3.2, C4.2, C5.2, C6.2, C7.2, C8.2, C9.2, C10.2, C11.2, C12.2, C13.2, C14.2, C15.2, C16.2, C17.2, C18.2, C19.2, C20.2, C21.2, C22.2, C23.1, C24.1, C25.1, C26.1, C27.1, C28.1, C29.1, C30.1, C31.2, C32.2, C33.2, C34.2, C35.2, C36.2, C37.2, C38.2, C39.2, C40.2, C41.2, C42.2, C43.2, C44.2, C45.2, C46.2, C47.2, C48.2, D1.1 (K), D2.1 (K), J1.3, J2.3, J3.3, J4.3, J6.2, J6.MP (MountPin), J7.1, J7.3, J8.1, J8.3, J9.1, J9.3, J26.1, J26.2, J26.5, J26.6, J26.9, J26.10, J27.1, J27.2, J27.5, J27.6, J27.9, J27.10, R4.2, R6.2, R8.2, R10.2, R12.2, R14.2, R16.2, R18.2, U1.8 (GND), U2.4 (~G2A), U2.8 (GND), U3.4 (~G2A), U3.8 (GND), U4.1 (GND), U5.1 (GND), U6.1 (GND), U7.1 (GND), U8.1 (GND), U9.1 (GND), U10.1 (GND), U11.1 (GND), U12.4 (GND), U13.5 (GND), U13.9 (PGND), U14.5 (GND), U14.9 (PGND), U15.5 (GND), U15.9 (PGND), U16.5 (GND), U16.9 (PGND), U17.5 (GND), U17.9 (PGND), U18.5 (GND), U18.9 (PGND), U19.5 (GND), U19.9 (PGND), U20.5 (GND), U20.9 (PGND), U21.5 (GND), U21.9 (PGND), U22.5 (GND), U22.9 (PGND), U23.5 (GND), U23.9 (PGND), U24.5 (GND), U24.9 (PGND), U25.5 (GND)
unnamed: D1.2 (A), R1.1
unnamed: D2.2 (A), R2.1
RFID_1_CS: A1.9 (D6), J1.8
RFID_2_CS: A1.10 (D7), J2.8
RFID_3_CS: A1.11 (D8), J3.8
RFID_4_CS: A1.12 (D9), J4.8
RFID_RESET: A1.13 (D10), J1.2, J2.2, J3.2, J4.2

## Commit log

2023-01-14 silkscreen & pad changes
    [i2c_repeater.kicad_sch, kato-switch-board.kicad_pcb, kato-switch-board.kicad_sch]
2023-01-14 use only rounded pads
    [kato-switch-board.kicad_pcb, kato-switch-board.kicad_sch, shift_led_driver.kicad_sch]
